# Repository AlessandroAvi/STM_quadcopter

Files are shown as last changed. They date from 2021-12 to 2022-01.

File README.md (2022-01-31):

# STM quadcopter

STILL WORK IN PROGRESS

This repository contains the code that I am developing for the creation of a quadcopter controller. The idea is to use a nucleo STM32 F401RE as the drone controller in order to control correctly each ESC, the accelerometer/gyre and the transmission between user and STM.

This project is inspired by another STM quadcopter developed some years ago by Brokking [here](http://www.brokking.net/ymfc-32_main.html) the link to its webiste and [here](https://www.youtube.com/user/MacPuffdog) the link to his video tutorials.

# BOM

| **COMPONENT** | **MODEL** | **N OF PIECES** | **COST €**| **LINK** |
| --- |:---:|:---:|:---:| ---:|
| Microcontroller | STM32 F411 | 1 | 6.68 | [here](https://it.aliexpress.com/item/32792513237.html?spm=a2g0s.9042311.0.0.74a34c4dBViBGv)
| ST link | - | 1 | 3.45 | [here](https://it.aliexpress.com/item/32792513237.html?spm=a2g0s.9042311.0.0.74a34c4dBViBGv)
| ESC + motor + propeller | 10000 kV - A2212 | 4 | 26.23 | [here](https://it.aliexpress.com/item/4000443619541.html?spm=a2g0s.9042311.0.0.27424c4d62Gi67)
| Battery connector | XT 60 male/female | 1 | 2.42 | [here](https://it.aliexpress.com/item/33004745121.html?spm=a2g0s.9042311.0.0.27424c4dqASuNE)
| Lipo Battery | 2200 mAh - 11.1 V - 3S - 30C | 1 | 20.99 | [here](https://www.amazon.it/gp/product/B08H861N2P/ref=ppx_yo_dt_b_asin_title_o05_s00?ie=UTF8&psc=1)
| Battery charger | 3S - B3 Pro | 1 | 4.15 | [here](https://it.aliexpress.com/item/4000917057193.html?spm=a2g0s.9042311.0.0.27424c4dGhvzAx)
| Gyroscope/IMU | MPU 6050 | 1 | 2.70 | [here](https://www.ebay.it/itm/253105882143)
| NRF24 tx + antenna | NRF24L01 | 1 | 1.85 | [here](https://it.aliexpress.com/item/32272725011.html?spm=a2g0s.9042311.0.0.74a34c4dBViBGv)
| FPV camera | OV2640 2MP | 1 | 4.74 | [here](https://it.aliexpress.com/item/33046344720.html?spm=a2g0s.9042311.0.0.34784c4d8o1aSF)
| Bluetooth receiver | HC-05 | 1 | 3.05 | [here](https://it.aliexpress.com/item/1005001636656116.html?spm=a2g0s.9042311.0.0.27424c4d7co4l5)
| GPS | GY-NEO6MV2 | 1 | 2.97 | [here](https://it.aliexpress.com/item/1005001635722164.html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)
| PCB for flight cntrl | - | 1 | - | [no link]()

Total cost up to now: 79.23 €

Just for initial prototyping I am controlling the drone actions with bluetooth. I am using an HC-05 bluetooth device connected to the STM and I send the control from an adroid app on my phone (arduino bluetooth controller). The app allows me to map to each button on the joystick a specific character. Future implementatios is to use a radio transmitter made with another STM that uses an NRF module.

Tutorials for the complementary filter and kalman filter at [here](https://www.youtube.com/watch?v=BUW2OdAtzBw).
A very nice tool that shows real time signal coming from the COM port [serial oscilloscope](https://x-io.co.uk/serial-oscilloscope/)

# TO DO

- Implement computation of angle from gyro data/ signal processing
- Tune correctly PD/PID
- Migrate all the code and project to a STM32 Blackpill (STM32 F10F411) + custom PCB
- create 3d model of frame + print

Useful link for sensor fusion between gyro and accelerometer with kalman filter 
 [here](https://www.telesens.co/2017/05/02/sensor-fusion-part-3-implementation-of-gyro-accel-sensor-fusion/)

# SITUATION UP TO NOW

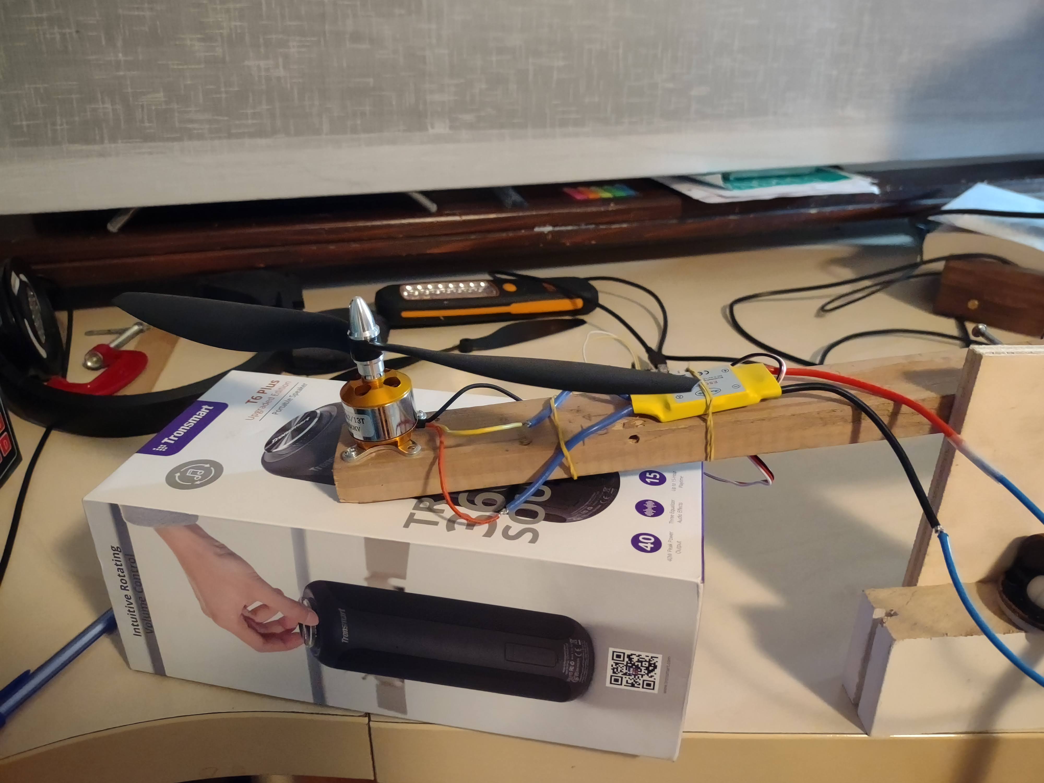
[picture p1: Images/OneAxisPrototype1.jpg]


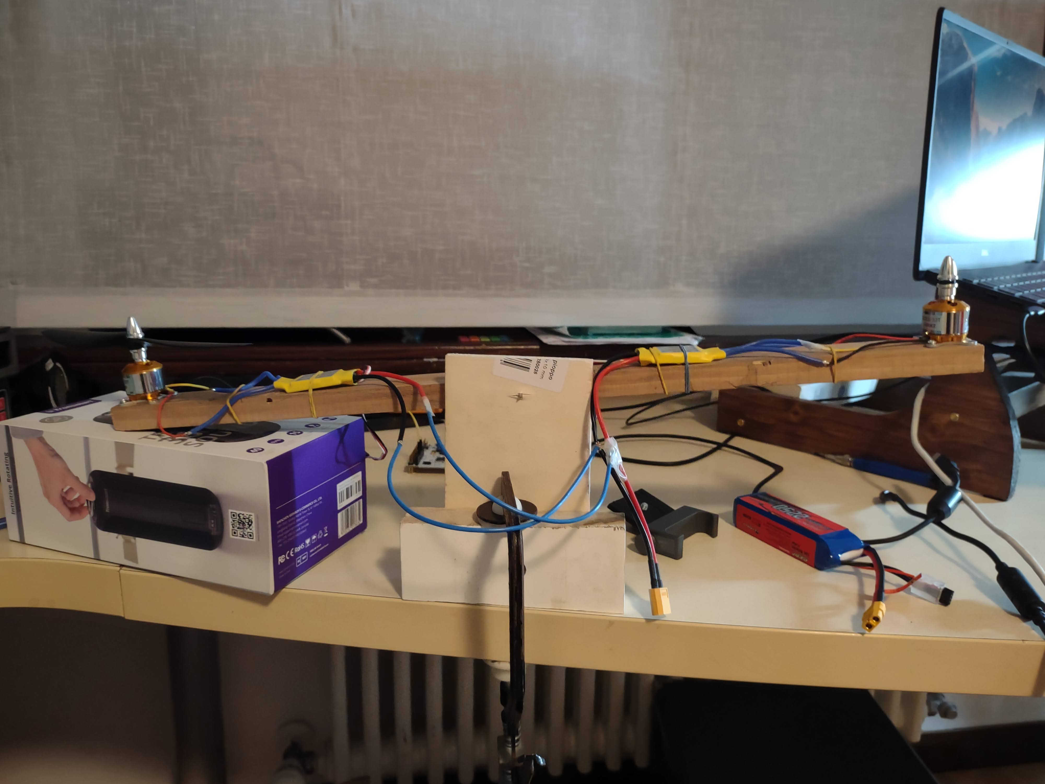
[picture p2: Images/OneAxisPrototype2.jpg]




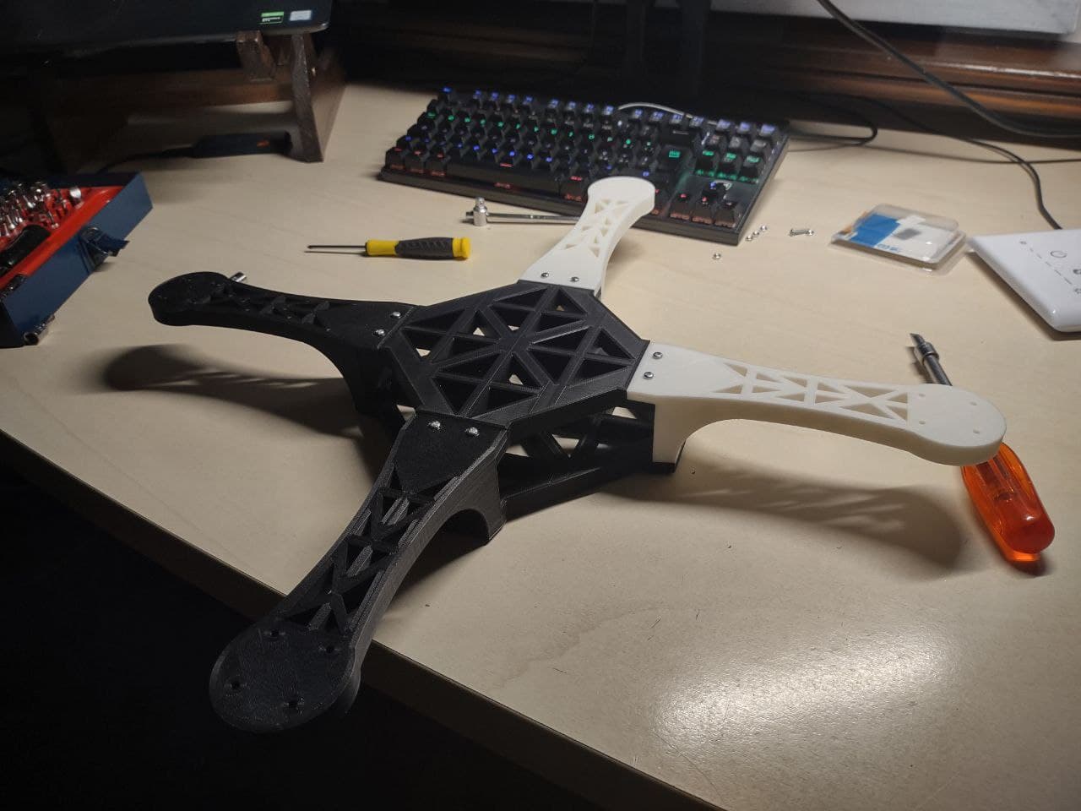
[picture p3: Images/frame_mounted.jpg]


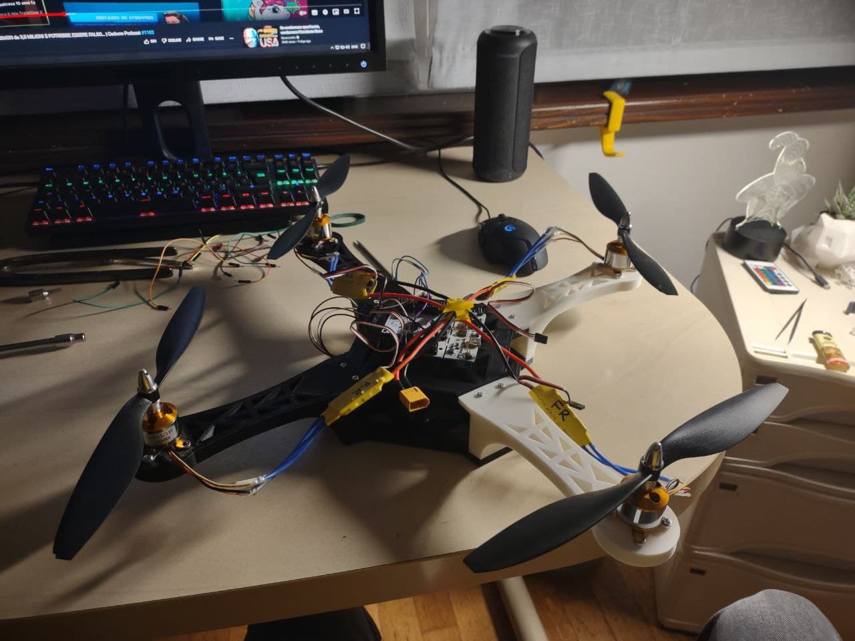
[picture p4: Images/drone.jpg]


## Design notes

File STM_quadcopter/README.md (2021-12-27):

# STM quadcopter

This repo contains the code developed for the flight controller. In this README.md file the explanation of the general idea of the code can be found.

## Explanation of the motors

The quadcopter is equipped with 4 brushless motors of 1000 KV. These are mopre than enough for making the frame lift and fly the vehicle. For the control of the motors speed a PWM signal is required. In this project it has been decided to not use directly a receiver for the control of the PWM, but rather generate the signal from the microcontroller depenging on the command received. From the datasheet is specified that the motors require a PWM signal at 50-60 Hz and the PWM signal should change in between the values of 1 ms for lowest speed and 2 ms for highest speed. If the motors are connected to a new device for the first time is good practice to teach them the throttle ranege that is going to be used. For doing this follow the [instructions](https://github.com/AlessandroAvi/STM_quadcopter/blob/main/Docs/datasheet_ESC.pdf) at page 3. In this project the source clock is of 84 MHz, the Timer 3 is used for the PWM signal with, prescaler = 70-1, ARR=20000-1 wich creates a PWM signal at 60 Hz. This set up allows me to have a resolution in between 1 ms and 2 ms of 1200 steps. 

## Explanation of MPU6050 

[Useful video tutorial](https://www.youtube.com/watch?v=RZd6XDx5VXo&t=0s)

The quadcopter is equipped with a MPU6050 board cwhich contains a gyroscope and an acceelrometer. The usage of these 2 sensors is more than enought for having a precise estimation of the pitch and roll angles that allows the drone to balance itself. In the code two methods of sensor fusion are develoepd, which are a bsic complementary filtering and a kalmann filter. 

The sensor fusion is required because the sensors taken alone are not reliable and subject to specific problems. The accelerometer is very sensible to noise and its values can be used for the computation of an angle only in the case the system is still with low vibrations. An accelerometer is reliable at low frequencies. On the other hand the gyroscope is able to give a precise measure of the angular rate, this means that in order to obtain an angle an integration is required. Since the raw measure is subject to noise and bias, the integration of the raw data will mose ptobably output an angle that is also subject to drift. The gyroscope is reliable at high frequencies. 

In order to get the best of both worlds it's a good idea to fuse the measuraments with eother a kalmann filter or a complementary filter. 

### Complementary filter

[Useful video tutorial](https://www.youtube.com/watch?v=BUW2OdAtzBw)

### Kalmann filter

[Useful video tutorial](https://www.youtube.com/watch?v=hQUkiC5o0JI)

### Explanation of NRF24 tx/rx data streaming

### Explanation of FPV camera

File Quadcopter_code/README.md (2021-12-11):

# Quadcopter code

This file contains informations about the code developed for teh flight controller.

This is the pin table for the STM32 blackpill F411CEU

| **STM PIN** |**FLIGHT CONTROLLER ROLE**| **DEVICE PIN** | 
| --- |:---:| --- |
| PA2 | USART 2 TX | PC USB | 
| PA3 | USART 2 RX | PC USB | 
| PA6 | TIM3 CH1 - PWM - FR fan  | FR ESC white cable | 
| PA7 | TIM3 CH2 - PWM - FL fan  | FL ESC white cable | 
| PB0 | TIM3 CH3 - PWM - RR fan  | RR ESC white cable | 
| PB1 | TIM3 CH4 - PWM - RL fan  | RL ESC white cable | 
| PA11 | USART 6 TX | HC-05 RX pin | 
| PA12 | USART 6 RX | HC-05 TX pin | 
| GND | HC-05 GND | HC-05 GND pin | 
| 5V | HC-05 VDD | HC-05 VDD pin | 
| GND | 4 ESC GND | ESC GND - black cable|

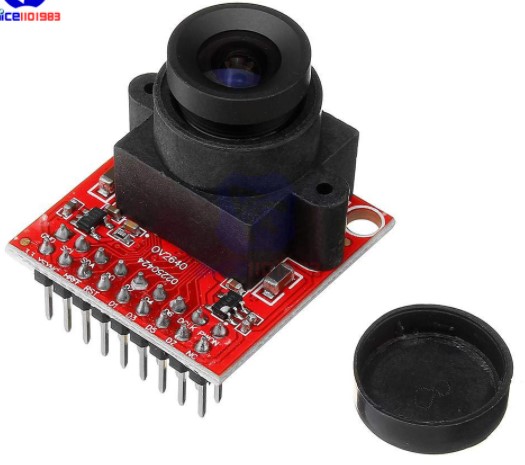
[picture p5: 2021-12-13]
Images/camera.jpg

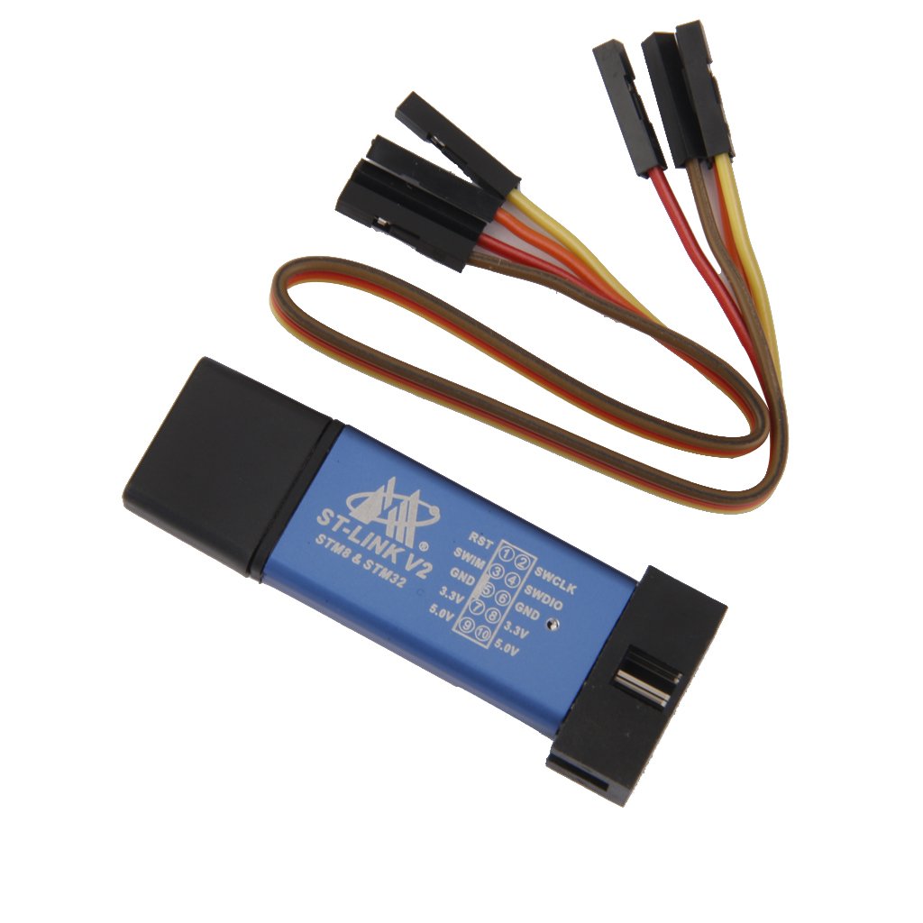
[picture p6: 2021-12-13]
Images/ST_link_v2.jpg

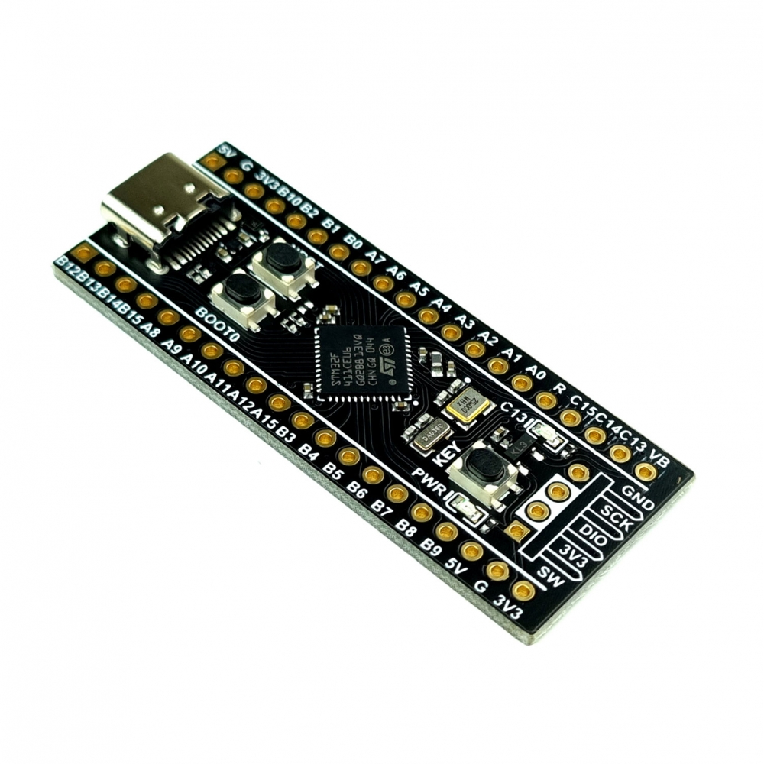
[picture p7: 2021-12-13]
Images/blackpill.jpg

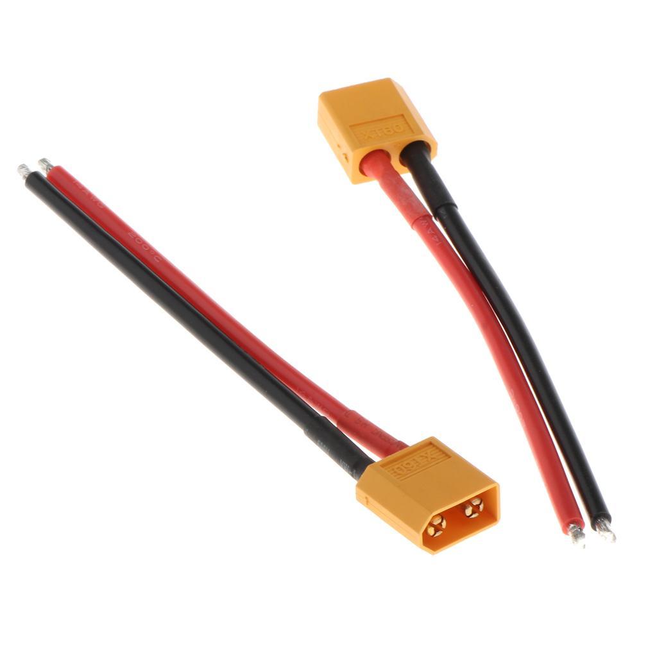
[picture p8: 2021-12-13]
Images/xt_60.jpg

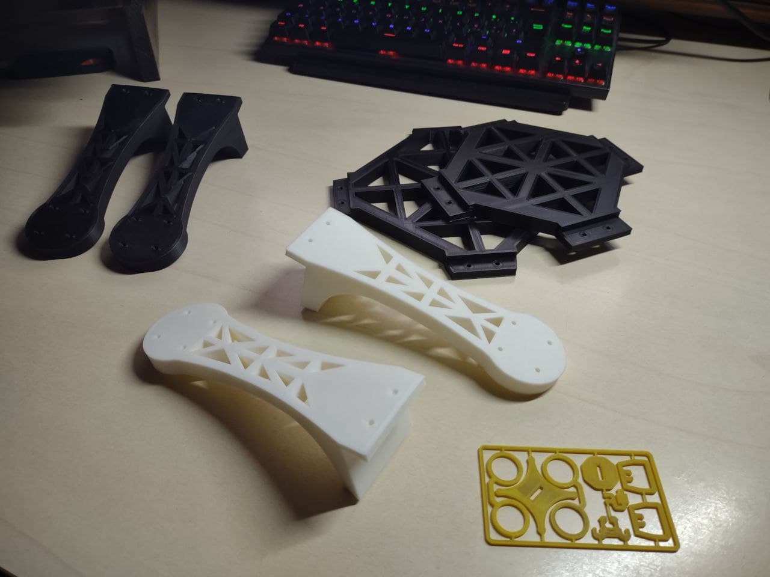
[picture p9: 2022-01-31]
Images/frame.jpg

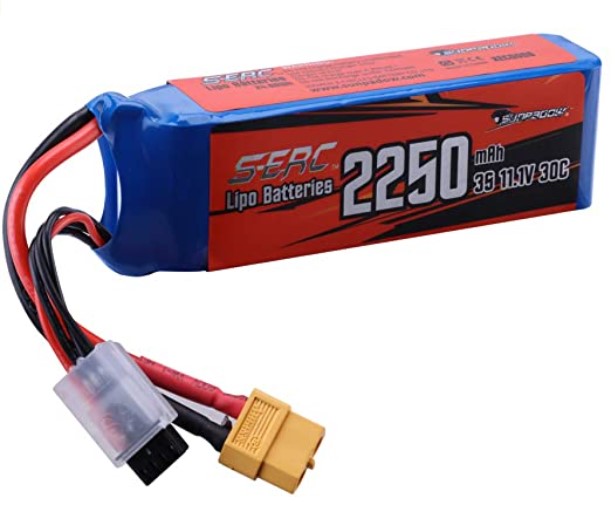
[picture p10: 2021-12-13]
Images/battery.jpg

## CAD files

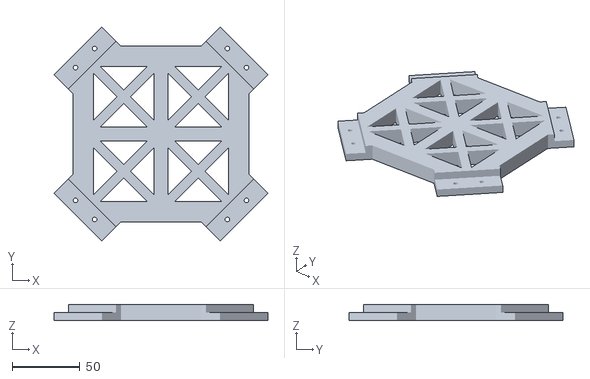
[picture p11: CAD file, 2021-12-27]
STL/quadcopter_base_high.stl
158.3 x 158.3 x 12.0

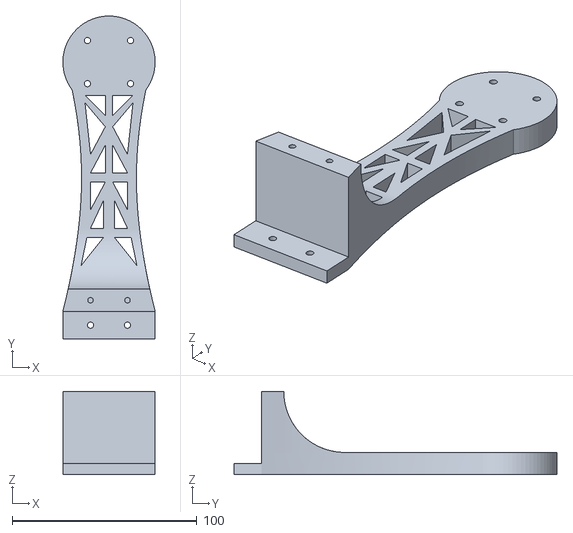
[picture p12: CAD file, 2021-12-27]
STL/quadcopter_arm.stl
50.0 x 175.0 x 45.0

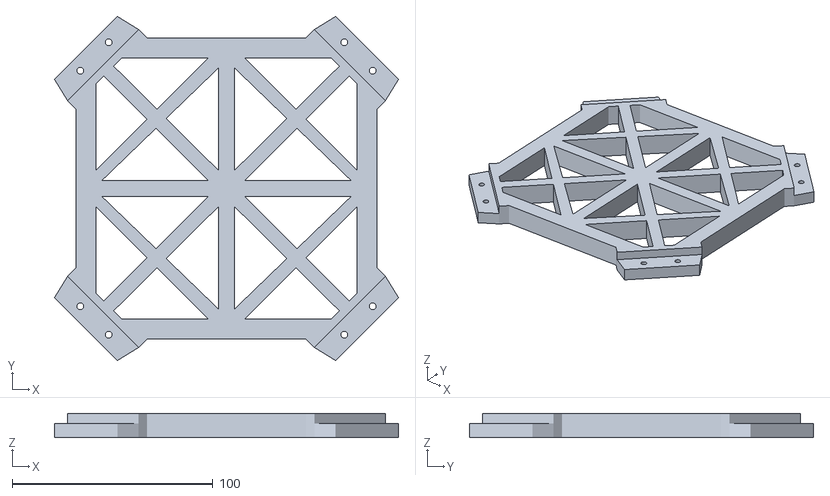
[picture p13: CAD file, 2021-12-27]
STL/quadcopter_base_low.stl
171.2 x 171.2 x 12.0

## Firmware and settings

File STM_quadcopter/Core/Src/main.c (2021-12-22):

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
/* Includes ------------------------------------------------------------------*/
#include "main.h"
#include "i2c.h"
#include "tim.h"
#include "usart.h"
#include "gpio.h"

/* USER CODE BEGIN Includes */
#include <stdio.h>
#include <string.h>

// My libraries
#include "ESC_ctrl.h"
#include "debug.h"
/* USER CODE END Includes */

/* USER CODE BEGIN PD */
#define RX_MSG_LEN 3
/* USER CODE END PD */


/* USER CODE BEGIN PV */

// DEBUG MESSAGES

// RECEIVE INFO MESSAGE
uint8_t msgRx[RX_MSG_LEN];

//Define flags
int BLUE_BUTTON = 0;
int BLUETOOTH_FLAG = 0;

// CONTAINERS
int dutyCycle = 0;
int dummy=0;


IMU_MEASURE MPU_measure;


/* USER CODE END PV */

void SystemClock_Config(void);
/**
  * @brief  The application entry point.
  * @retval int
  */
int main(void)
{
  /* MCU Configuration--------------------------------------------------------*/

  /* Reset of all peripherals, Initializes the Flash interface and the Systick. */
  HAL_Init();

  /* Configure the system clock */
  SystemClock_Config();

  /* Initialize all configured peripherals */
  MX_GPIO_Init();
  MX_USART2_UART_Init();
  MX_USART6_UART_Init();
  MX_TIM3_Init();
  MX_I2C1_Init();
  MX_TIM10_Init();
  /* USER CODE BEGIN 2 */

  //PRINTF("\n\r BEGINNING OF THE CODE \n\n\r");

  // Start timer interrupt that enables the GYRO reading 250 Hz
  HAL_TIM_Base_Start_IT(&htim10);

  // Start timer for the PWM signal
  HAL_TIM_PWM_Start(&htim3, TIM_CHANNEL_1);
  HAL_TIM_PWM_Start(&htim3, TIM_CHANNEL_2);
  HAL_TIM_PWM_Start(&htim3, TIM_CHANNEL_3);
  HAL_TIM_PWM_Start(&htim3, TIM_CHANNEL_4);

  // Start interrupt for bluetooth Rx commands
  HAL_UART_Receive_IT(&huart6, (uint8_t*)cmd_rx, 1);

  ESC_CONF ESC_speed;

  ESC_Calibrate(&ESC_speed);

  //PRINTF(" -- Press blue button to start the code \n\n\r");
  while(BLUE_BUTTON==0){
	  if(BLUE_BUTTON==1){
		  break;
	  }
  }

  MPU6050_Init();
  MPU6050_Reset(&MPU_measure);

  ESC_Init(&ESC_speed);





  /* USER CODE END 2 */

  /* Infinite loop */
  /* USER CODE BEGIN WHILE */
  while (1)
  {

	  if(ACC_STATE == READY && GYRO_STATE == READY){
		  //int lengh = sprintf(messaggio, "ACC: x %f, y %f \n\r FL %d  -  FR %d  -  RL %d - RR %d \r\n", MPU_measure.angle_X, MPU_measure.angle_Y, ESC_speed.FL, ESC_speed.FR, ESC_speed.RL, ESC_speed.RR);
		  //HAL_UART_Transmit(&huart2, (uint8_t*)messaggio, lengh, 50);
	  }


	  // Receive the command from the radio/bl controller
	  if(BLUETOOTH_FLAG == 1){

		  //msgLen = sprintf(msgDebug, "\n\r   FRONTT LEFT %d  -  FRONT RIGHT %d  -  REAR LEFT %d - REAR RIGHT %d \r\n", ESC_speed.FL, ESC_speed.FR, ESC_speed.RL, ESC_speed.RR);
		  //HAL_UART_Transmit(&huart2, (uint8_t*)msgDebug, msgLen, 10);

		  BLUETOOTH_FLAG = 0;
	  }else{
		  cmd_rx[0] = ' ';
	  }

	  ESC_followCmd(&ESC_speed, &MPU_measure, cmd_rx[0]);
	  ESC_setSpeed(&ESC_speed);

	  //msgLen = sprintf(msgDebug, "\r CIAO");
	  //HAL_UART_Transmit(&huart2, (uint8_t*)msgDebug, msgLen, 10);

		char message[50];
		int length = 0;

		length = sprintf(message, "%f, %f, %f \r", MPU_measure.angle_X, MPU_measure.angle_Y, MPU_measure.angle_Z);
		HAL_UART_Transmit(&huart2, (uint8_t*)message, length, 10);


    /* USER CODE END WHILE */

    /* USER CODE BEGIN 3 */
  }
  /* USER CODE END 3 */
}

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
/* USER CODE BEGIN 4 */



// Interrupt from the timer
void HAL_TIM_PeriodElapsedCallback(TIM_HandleTypeDef *htim){

	if(htim == &htim10){
		MPU6050_ReadAcc(&MPU_measure);
		MPU6050_ReadGyro(&MPU_measure);
		MPU6050_ComplementFilter(&MPU_measure);
	}
}


// Interrupt from bluetooth
void HAL_UART_RxCpltCallback(UART_HandleTypeDef * huart){

	if(BLUETOOTH_FLAG==0){
		BLUETOOTH_FLAG = 1;
	}

	HAL_UART_Receive_IT(&huart6, (uint8_t*)cmd_rx, 1);
}


void HAL_GPIO_EXTI_Callback(uint16_t GPIO_Pin){

	if(GPIO_Pin == B1_Pin){
		if(BLUE_BUTTON == 0){
			BLUE_BUTTON=1;
		}
	}

}



/* USER CODE END 4 */
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


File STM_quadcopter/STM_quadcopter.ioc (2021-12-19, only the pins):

Mcu.UserName=STM32F401RETx
PA13.GPIO_Label=TMS
PA13.Signal=SYS_JTMS-SWDIO
PA14.GPIO_Label=TCK
PA14.Signal=SYS_JTCK-SWCLK
PA2.GPIO_Label=USART_TX
PA2.Signal=USART2_TX
PA3.GPIO_Label=USART_RX
PA3.Signal=USART2_RX
PA5.GPIO_Label=LD2 [Green Led]
PA5.Signal=GPIO_Output
PA6.Signal=S_TIM3_CH1
PA7.Signal=S_TIM3_CH2
PB0.Signal=GPIO_Output
PB1.Signal=S_TIM3_CH4
PB3.GPIO_Label=SWO
PB3.Signal=SYS_JTDO-SWO
PB6.Signal=I2C1_SCL
PB7.Signal=I2C1_SDA
PC13-ANTI_TAMP.GPIO_Label=B1 [Blue PushButton]
PC13-ANTI_TAMP.Signal=GPXTI13
PC14-OSC32_IN.Signal=RCC_OSC32_IN
PC15-OSC32_OUT.Signal=RCC_OSC32_OUT
PC6.Signal=USART6_TX
PC7.Signal=USART6_RX
PC8.Signal=S_TIM3_CH3

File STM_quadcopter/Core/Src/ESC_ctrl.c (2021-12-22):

#include "ESC_ctrl.h"
#include "tim.h"



char cmd_rx[1];


// FUNCTIONS *****************************
void ESC_Init(ESC_CONF * ESC_speed){

	  ESC_speed->FR = 0;
	  ESC_speed->FL = 0;
	  ESC_speed->RR = 0;
	  ESC_speed->RL = 0;

	  ESC_speed->state = ARMED;

	  ESC_speed->up_value = 0;

	  // Set PWM to 0 for the ESC (1 ms)
	  TIM3->CCR1 = ESC_speed->FR + PWM_1_MS;
	  TIM3->CCR2 = ESC_speed->FL + PWM_1_MS;
	  TIM3->CCR3 = ESC_speed->RR + PWM_1_MS;
	  TIM3->CCR4 = ESC_speed->RL + PWM_1_MS;
}

void ESC_Calibrate(ESC_CONF * ESC_speed){

	  TIM3->CCR1 = PWM_1_MS;
	  TIM3->CCR2 = PWM_1_MS;
	  TIM3->CCR3 = PWM_1_MS;
	  TIM3->CCR4 = PWM_1_MS;

	  ESC_speed->state = DISARMED;
}


void ESC_followCmd(ESC_CONF * ESC_speed, IMU_MEASURE * MPU_measure, char cmd){

	int cmd_pitch = 0;
	int cmd_roll  = 0;

	int16_t low_lim = 0;
	int16_t high_lim = 600;

	// PID values
	int P_pitch = 2;
	int D_pitch  = 1;
	//int I_pitch = 0;
	int P_roll  = 2;
	int D_roll  = 1;
	//int I_roll = 0;


	if(cmd == 'W'){	// forward
		cmd_pitch = -10;
		//PRINTF(" FORWARD \n\r");
	}else if(cmd == 'A'){ // left
		cmd_roll = -10;
		//PRINTF(" LEFT \n\r");
	}else if(cmd == 'S'){ // back
		cmd_pitch = 10;
		//PRINTF(" BACK \n\r");
	}else if(cmd == 'D'){ // right
		cmd_roll = +10;
		//PRINTF(" RIGHT \n\r");
	}else if(cmd == 'I'){ // up
		ESC_speed->up_value += 10;
		//PRINTF(" UP \n\r");
	}else if(cmd == 'J'){ // rotate left
		//PRINTF(" ROT LEFT \n\r");
	}else if(cmd == 'K'){ // down
		ESC_speed->up_value -= 50;
		//PRINTF(" DOWN \n\r");
	}else if(cmd == 'L'){ // rotate right
		//PRINTF(" ROT RIGHT \n\r");
	}else if(cmd == 'X'){ // disarm drone
		ESC_speed->state = DISARMED;
		//PRINTF(" DISARM \n\r");
	}else if(cmd == 'C'){ // arms DRONE
		ESC_speed->state = ARMED;
		//PRINTF(" ARM \n\r");
	}

	// Security check to avoid dead bodies in the field
	if(MPU_measure->angle_X > 10 || MPU_measure->angle_Y > 10 || MPU_measure->angle_X < -10 || MPU_measure->angle_Y < -10){
		ESC_speed->state == DISARMED;
	}

	if(ESC_speed->state == ARMED){

		double pitch_err   = 0;//cmd_pitch - MPU_measure->angle_X;
		double pitch_d_err = 0;//MPU_measure->gyro_angle_dX;

		double roll_err    = 0;//cmd_roll  - MPU_measure->angle_Y;
		double roll_d_err  = 0;//MPU_measure->gyro_angle_dY;

		int16_t FR_tmp = ESC_speed->up_value + pitch_err*P_pitch - pitch_d_err*D_pitch - roll_err*P_roll + roll_d_err*D_roll;
		int16_t FL_tmp = ESC_speed->up_value + pitch_err*P_pitch - pitch_d_err*D_pitch + roll_err*P_roll - roll_d_err*D_roll;
		int16_t RR_tmp = ESC_speed->up_value - pitch_err*P_pitch + pitch_d_err*D_pitch - roll_err*P_roll + roll_d_err*D_roll;
		int16_t RL_tmp = ESC_speed->up_value - pitch_err*P_pitch + pitch_d_err*D_pitch + roll_err*P_roll - roll_d_err*D_roll;

		if(FR_tmp > low_lim && FR_tmp < high_lim){
			ESC_speed->FR = FR_tmp;
		}

		if(FL_tmp > low_lim && FL_tmp < high_lim){
			ESC_speed->FL = FL_tmp;
		}

		if(RR_tmp > low_lim && RR_tmp < high_lim){
			ESC_speed->RR = RR_tmp;
		}

		if(RL_tmp > low_lim && RL_tmp < high_lim){
			ESC_speed->RL = RL_tmp;
		}

	}else if(ESC_speed->state == DISARMED){

		ESC_speed->FR = 0;
		ESC_speed->FL = 0;
		ESC_speed->RR = 0;
		ESC_speed->RL = 0;
		ESC_speed->up_value =0;
	}
}


void ESC_setSpeed(ESC_CONF * ESC_speed){

	TIM3->CCR1 = ESC_speed->FR + PWM_1_MS;
	TIM3->CCR2 = ESC_speed->FL + PWM_1_MS;
	TIM3->CCR3 = ESC_speed->RR + PWM_1_MS;
	TIM3->CCR4 = ESC_speed->RL + PWM_1_MS;
}

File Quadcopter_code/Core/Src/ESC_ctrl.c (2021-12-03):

#include "ESC_ctrl.h"
#include "tim.h"



char cmd_rx[1];


// FUNCTIONS *****************************

void ESC_setSpeed(ESC_STATUS * ESC_speed){

	TIM3->CCR1 = ESC_speed->FR + 1000;
	TIM3->CCR2 = ESC_speed->FL + 1000;
	TIM3->CCR3 = ESC_speed->RR + 1000;
	TIM3->CCR4 = ESC_speed->RL + 1000;


	  if(ESC_speed->FL > 1000){
		  ESC_speed->FL = 1000;
	  }else if(ESC_speed->FL <= 0 || ESC_speed->FL > 1000){
		  ESC_speed->FL = 0;
	  }

	  if(ESC_speed->FR > 1000){
		  ESC_speed->FR = 1000;
	  }else if(ESC_speed->FR <= 0 || ESC_speed->FR >1000){
		  ESC_speed->FR = 0;
	  }

	  if(ESC_speed->RR > 1000){
		  ESC_speed->RR = 1000;
	  }else if(ESC_speed->RR <= 0 || ESC_speed->RR >1000){
		  ESC_speed->RR = 0;
	  }

	  if(ESC_speed->RL > 1000){
		  ESC_speed->RL = 1000;
	  }else if(ESC_speed->RL <= 0 || ESC_speed->RL >1000){
		  ESC_speed->RL = 0;
	  }


}




void CMD_transform(ESC_STATUS * ESC_speed, char cmd){

	int deltaFR = 0;
	int deltaFL = 0;
	int deltaRR = 0;
	int deltaRL = 0;
	int dummy = 0;
	int delta = 10;

	if(cmd == 'W'){	// forward
		deltaFR -= delta;
		deltaFL -= delta;
		deltaRR += delta;
		deltaRL += delta;

	}else if(cmd == 'A'){ // left
		deltaFR += delta;
		deltaFL -= delta;
		deltaRR += delta;
		deltaRL -= delta;

	}else if(cmd == 'S'){ // back
		deltaFR += delta;
		deltaFL += delta;
		deltaRR -= delta;
		deltaRL -= delta;

	}else if(cmd == 'D'){ // right
		deltaFR -= delta;
		deltaFL += delta;
		deltaRR -= delta;
		deltaRL += delta;

	}else if(cmd == 'I'){ // up
		deltaFR += delta;
		deltaFL += delta;
		deltaRR += delta;
		deltaRL += delta;

	}else if(cmd == 'J'){ // rotate left
		deltaFR += delta;
		deltaFL -= delta;
		deltaRR -= delta;
		deltaRL += delta;

	}else if(cmd == 'K'){ // down
		deltaFR -= delta;
		deltaFL -= delta;
		deltaRR -= delta;
		deltaRL -= delta;

	}else if(cmd == 'L'){ // rotate right
		deltaFR -= delta;
		deltaFL += delta;
		deltaRR += delta;
		deltaRL -= delta;

	}else if(cmd == 'X'){ // ?
		ESC_speed->FR = 0;
		ESC_speed->FL = 0;
		ESC_speed->RR = 0;
		ESC_speed->RL = 0;
		return;

	}else if(cmd == 'C'){ // ?

	}

	if(ESC_speed->FR==0 && deltaFR<0){
		dummy = 0;
	}else{
		ESC_speed->FR += deltaFR;
	}
	if(ESC_speed->FL==0 && deltaFL<0){
		dummy = 0;
	}else{
		ESC_speed->FL += deltaFL;
	}
	if(ESC_speed->RR==0 && deltaRR<0){
		dummy = 0;
	}else{
		ESC_speed->RR += deltaRR;
	}
	if(ESC_speed->RL==0 && deltaRL<0){
		dummy = 0;
	}else{
		ESC_speed->RL += deltaRL;
	}


}

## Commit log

2021-11-25 Code update
    Added function that sets up PWM correctly
    Added datasheet in the folder
    [ESC_ctrl.c, STM_quadcopter.ioc, main.c]
2021-11-25 Can control ESC easily
    Can define a number between 0 and 1 from UART and control the speed with this number
2021-11-27 ESC can be controlled from keyboard
2021-12-03 Manually tuned ESC + tested bluetooth controls
2021-12-13 Added Gyro code
2021-12-15 Added LPF design and self balance code
    Still self balance code needs to be tuned with only P
    Also need to remove gyro drift
    [ESC_ctrl.c, MPU6050.c, MPU6050.h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]
2021-12-19 Added accelerometer in angle measure
2021-12-19 Tested and debugged accel + gyro
2021-12-21 Tuned a bit complementary filter + security check over 10 deg
2021-12-21 Removed calibration at start time, pwm is now 0
2021-12-22 Fixed complementary filter
    [quadcopter_arm.stl, quadcopter_base_high.stl, quadcopter_base_low.stl]
2021-12-27 STL + images
    [quadcopter_arm.stl, quadcopter_base_high.stl, quadcopter_base_low.stl]

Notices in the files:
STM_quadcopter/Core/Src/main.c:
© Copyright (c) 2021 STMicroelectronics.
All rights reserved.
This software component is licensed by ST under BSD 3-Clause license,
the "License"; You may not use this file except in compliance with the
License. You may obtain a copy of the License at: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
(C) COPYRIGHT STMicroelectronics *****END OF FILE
